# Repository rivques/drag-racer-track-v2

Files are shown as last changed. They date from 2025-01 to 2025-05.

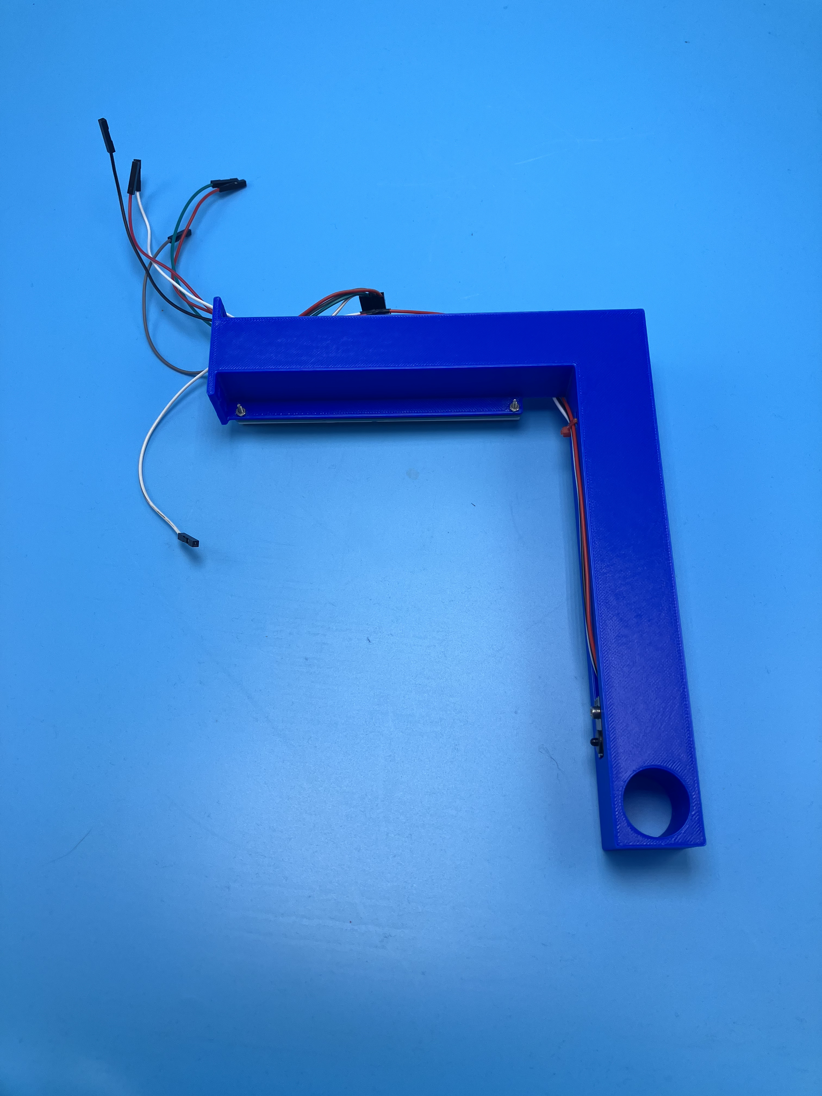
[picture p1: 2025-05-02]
doc-pics/end_cap_left_assembled_back.jpg

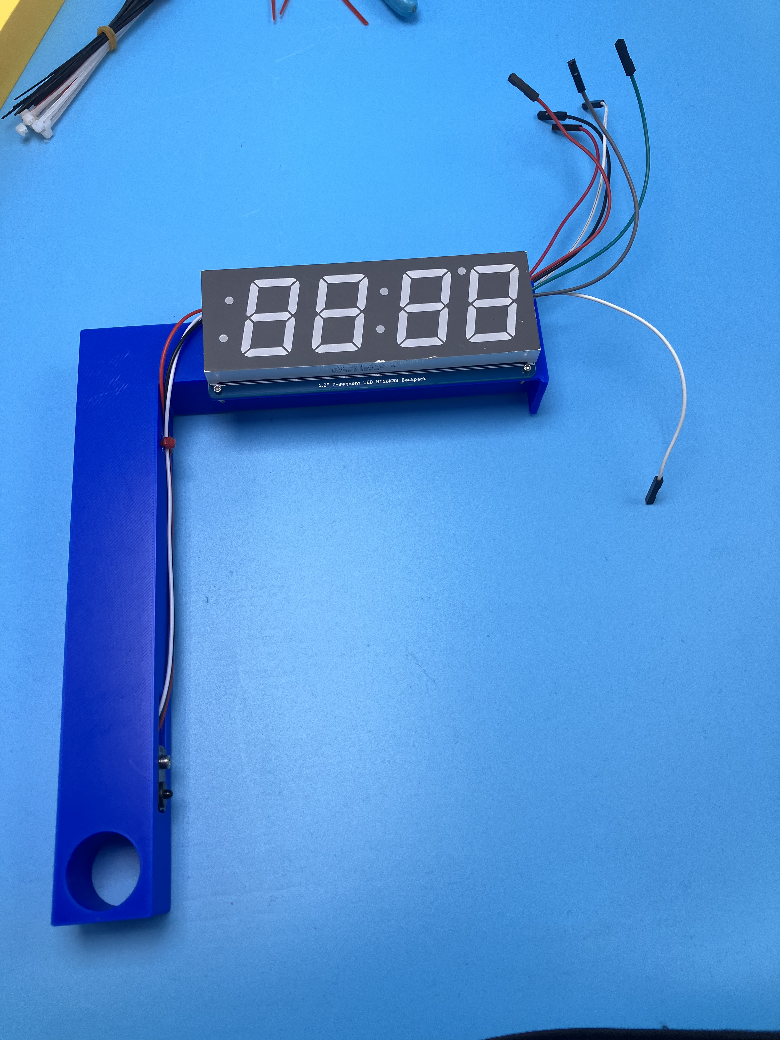
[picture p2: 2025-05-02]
doc-pics/end_cap_left_assembled_front.jpg

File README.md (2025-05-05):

# drag-racer-track-v2
A new and improved version of [mini-drag-racetrack](https://github.com/rivques/mini-drag-racetrack).
A photo of the complete assembly

## Contact Me
While this racetrack was designed to be maintainable by people other than me, please don't hesitate to contact me if you run into an issue that these docs don't cover.
You can open an issue on this repository, email me at `web (at) rivques (dot) dev`, or check [my website](https://rivques.dev) for my latest contact information.

## Troubleshooting
See [troubleshooting.md](docs/troubleshooting.md)

## How to Use
See [how_to_use.md](docs/how_to_use.md)

## Bill Of Materials
See [bill_of_materials.md](docs/bill_of_materials.md)

## Assembly From Storage
See [assembly_from_storage.md](docs/assembly_from_storage.md)

## Assembly From Scratch
See [assembly_from_scratch.md](docs/assembly_from_scratch.md)

## CAD
See [the CAD folder](https://github.com/rivques/drag-racer-track-v2/tree/main/cad) or [this Onshape document](https://cvilleschools.onshape.com/documents/214ca204c2fbd1332e8a9828/w/7c57c6410ddb9c7d8c5eff08/e/c34b4d3245393d7aa3c3b2bb).

## Project Proposal
Available at [this Google doc](https://docs.google.com/document/d/1fPM3jAb2btpLcQTNEUYPZXAGJ7guPSih1aArkj4l1_s/edit?usp=sharing), viewable from a CCS account.

## Photos
Various photos of the assembly are available in the [doc-pics](https://github.com/rivques/drag-racer-track-v2/tree/main/doc-pics) directory.

## Circuit Diagrams
Schematics and board layouts are available in the [circuit/outputs](https://github.com/rivques/drag-racer-track-v2/tree/main/circuit/outputs) directory.

### Commmunication
The three modules communicate over straight-through CAT-5 (aka Ethernet) cable. This pinout is constructed to allow near-unambiguous determination by the main processor of 1. if a cable is connected and 2. if the cable is connected to the motors or the screen.

The pinout is as follows (assuming T568A terminations):

#### Main-Motor (purpose and direction from Main's perspective):

RJ-45 Pin # | T568A color | Pico pin | Purpose | Direction | Notes
---|---|---|---|---|---
1|Wh/Gr|GND|GND|Bidirectional|Shared ground reference
2|Gr|GP0|TX|OUTPUT|UART 8N1@9600 baud
3|Wh/Or|GP2|Discrim|INPUT|Tied to GND at Motor
4|Bl|NC|NC||
5|Wh/Bl|3V3OUT|3V3|OUTPUT|
6|Or|GP1|RX|INPUT|UART 8N1@9600 baud
7|Wh/Br|GP3|Presence|INPUT|Tied to GND at Motor
8|Br|NC|NC||

#### Main-Button Controller (purpose and direction from Main's perspective):

RJ-45 Pin # | T568A color | Pico pin | Purpose | Direction | Notes
---|---|---|---|---|---
1|Wh/Gr|GND|GND|OUTPUT|
2|Gr|GP17|LED_RACE|OUTPUT|
3|Wh/Or|GP8|Discrim|INPUT|Tied to RESET at Controller
4|Bl|GP4|RESET|INPUT|
5|Wh/Bl|GP16|LED_ARM|OUTPUT|
6|Or|GP5|ARM|INPUT|
7|Wh/Br|GP7|Presence|INPUT|Tied to GND at Controller
8|Br|GP6|RACE|INPUT|

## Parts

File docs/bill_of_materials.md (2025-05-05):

# Bill of Materials

## Electronics

* 1x Mainboard PCB. For KiCad files, see the circuit directory of this repo.
* 2x [Adafruit beam-break 3mm sensors](https://www.adafruit.com/product/2167)
* 4x [SparkFun RJ45 breakouts](https://www.sparkfun.com/sparkfun-rj45-breakout.html) with [SparkFun RJ45 conectors](https://www.sparkfun.com/rj45-8-pin-connector.html)
* 2x [Adafruit 1.2" 4x7 segment LED displays w/ I2C backpack](https://www.adafruit.com/product/1269)
* 1x [Adafruit 1.3" OLED display](https://www.adafruit.com/product/938)
* 2x [SPDT breadboard switch](https://www.adafruit.com/product/805)
* 2x [Raspberry Pi Pico](https://www.adafruit.com/product/5525)
* 2x [1N4001 diodes](https://www.adafruit.com/product/755)
* 1x [7805 voltage regulator](https://www.adafruit.com/product/2164)
* 1x 0.22-0.33µF capacitor
* 1x 0.1µF capacitor
* 11x 220Ω resistors
* 5x single-color LEDs
* 3x [COMMON ANODE RGB LEDs](https://www.adafruit.com/product/302)
* 1x [2cm x 8cm perfboard](https://www.adafruit.com/product/4783)
* 1x [3cm x 7cm perfboard](https://www.adafruit.com/product/4784)
* 3x [12mm breadboard pushbuttons](https://www.adafruit.com/product/1119), with the bottom nubs snipped off so they lay flat
* 1x [Adafruit Perma-Proto Bonnet Mini](https://www.adafruit.com/product/3203)
* 2x [micro servos](https://www.adafruit.com/product/169)
* 1x [piezo buzzer](https://www.adafruit.com/product/160)
* 1x [4xAA battery holder](https://www.adafruit.com/product/3859)
* 1x 9V battery clip
* 2x Ethernet cables, one at least 13 feet long
* Assorted DuPont headers

## 3D-printed parts

From [the CAD folder](https://github.com/rivques/drag-racer-track-v2/tree/main/cad) or [this Onshape document](https://cvilleschools.onshape.com/documents/214ca204c2fbd1332e8a9828/w/7c57c6410ddb9c7d8c5eff08/e/c34b4d3245393d7aa3c3b2bb):

* end_cap_left
* end_cap_center
* end_cap_right
* start_cap_left
* start_cap_center
* start_cap_right

All of these should fit on a Prusa MK4S and can be printed out of PLA. Each should have a fairly obviously correct orientation. They shouldn't need supports.

## Other parts

* 12x #4-40 McMaster heat-set inserts
* Assorted 1/2in #4-40 standoffs
* Assorted #4-40 bolts (including button caps for the battery pack)

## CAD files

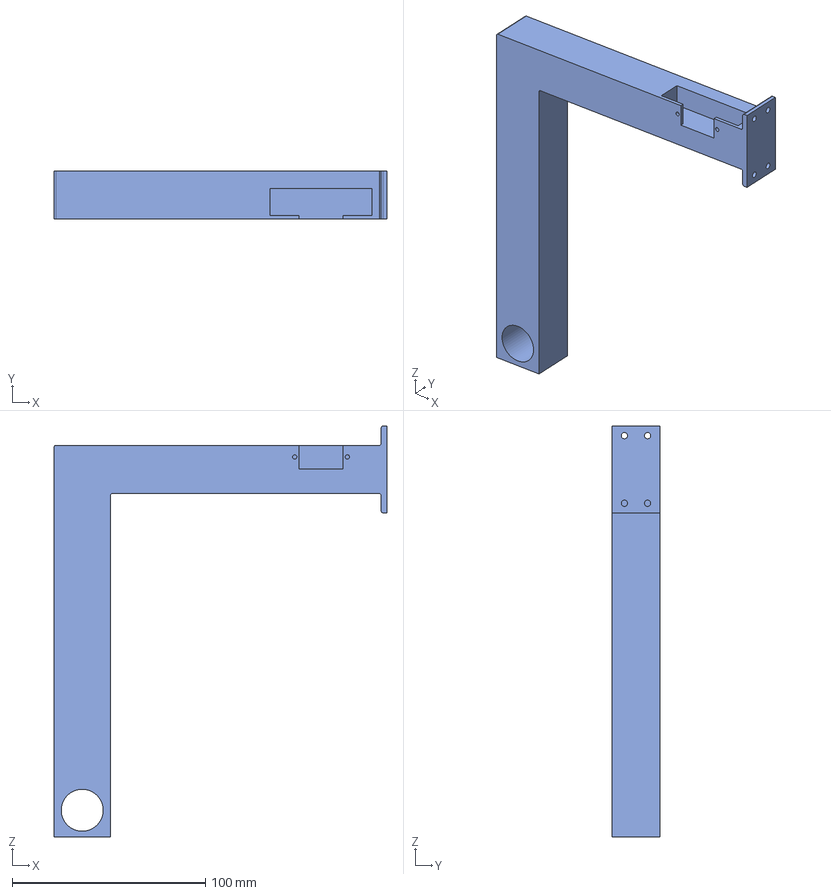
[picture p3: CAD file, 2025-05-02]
cad/start_cap_left.step
172.4 x 25.0 x 212.8 mm

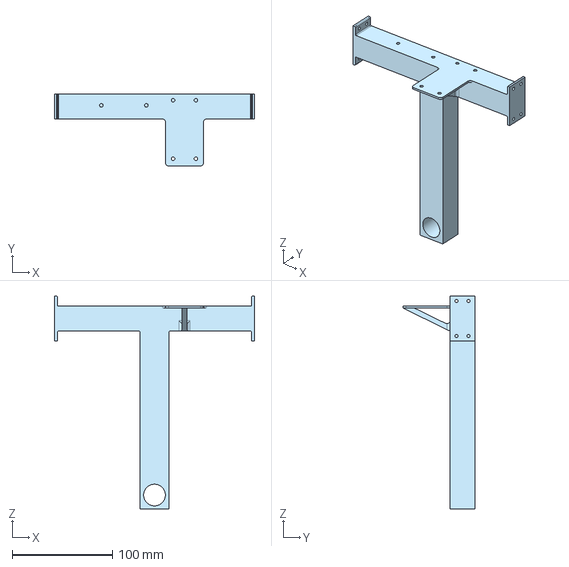
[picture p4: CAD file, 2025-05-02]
cad/start_cap_center.step
200.0 x 71.9 x 212.8 mm

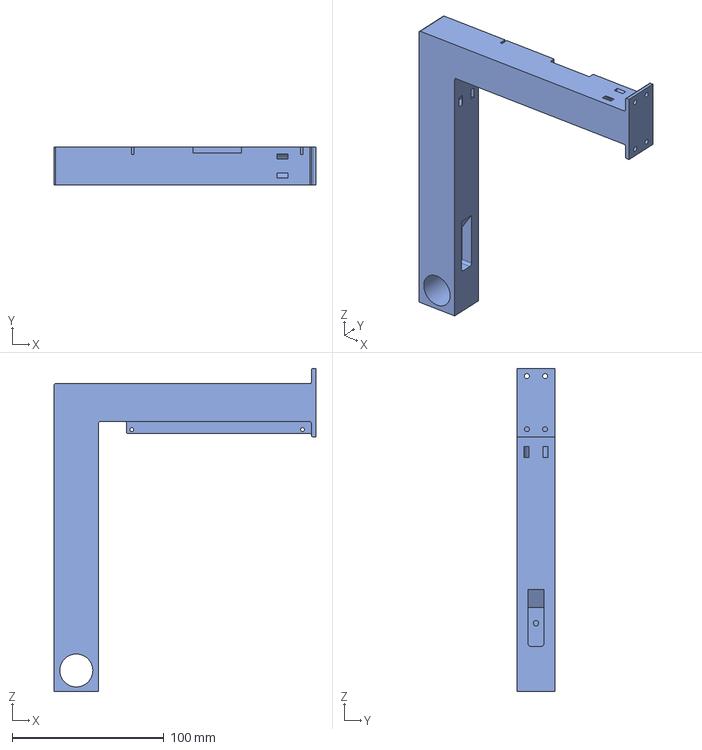
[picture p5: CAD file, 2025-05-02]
cad/end_cap_left.step
172.4 x 25.0 x 212.8 mm

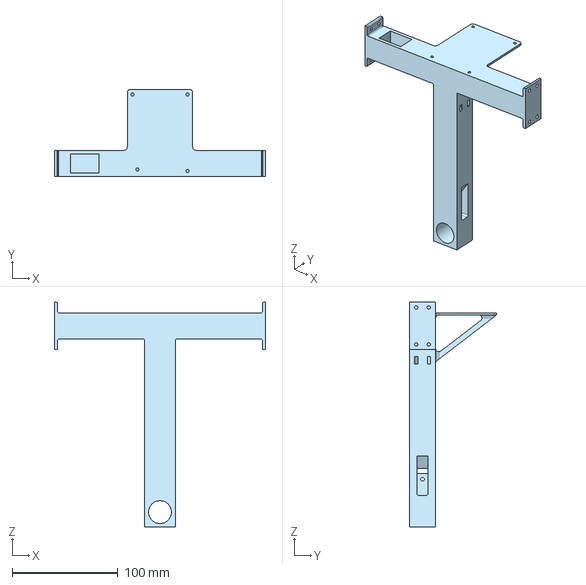
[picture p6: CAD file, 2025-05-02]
cad/end_cap_center.step
200.0 x 82.8 x 212.8 mm

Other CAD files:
cad/start_cap_right.step
cad/end_cap_right.step

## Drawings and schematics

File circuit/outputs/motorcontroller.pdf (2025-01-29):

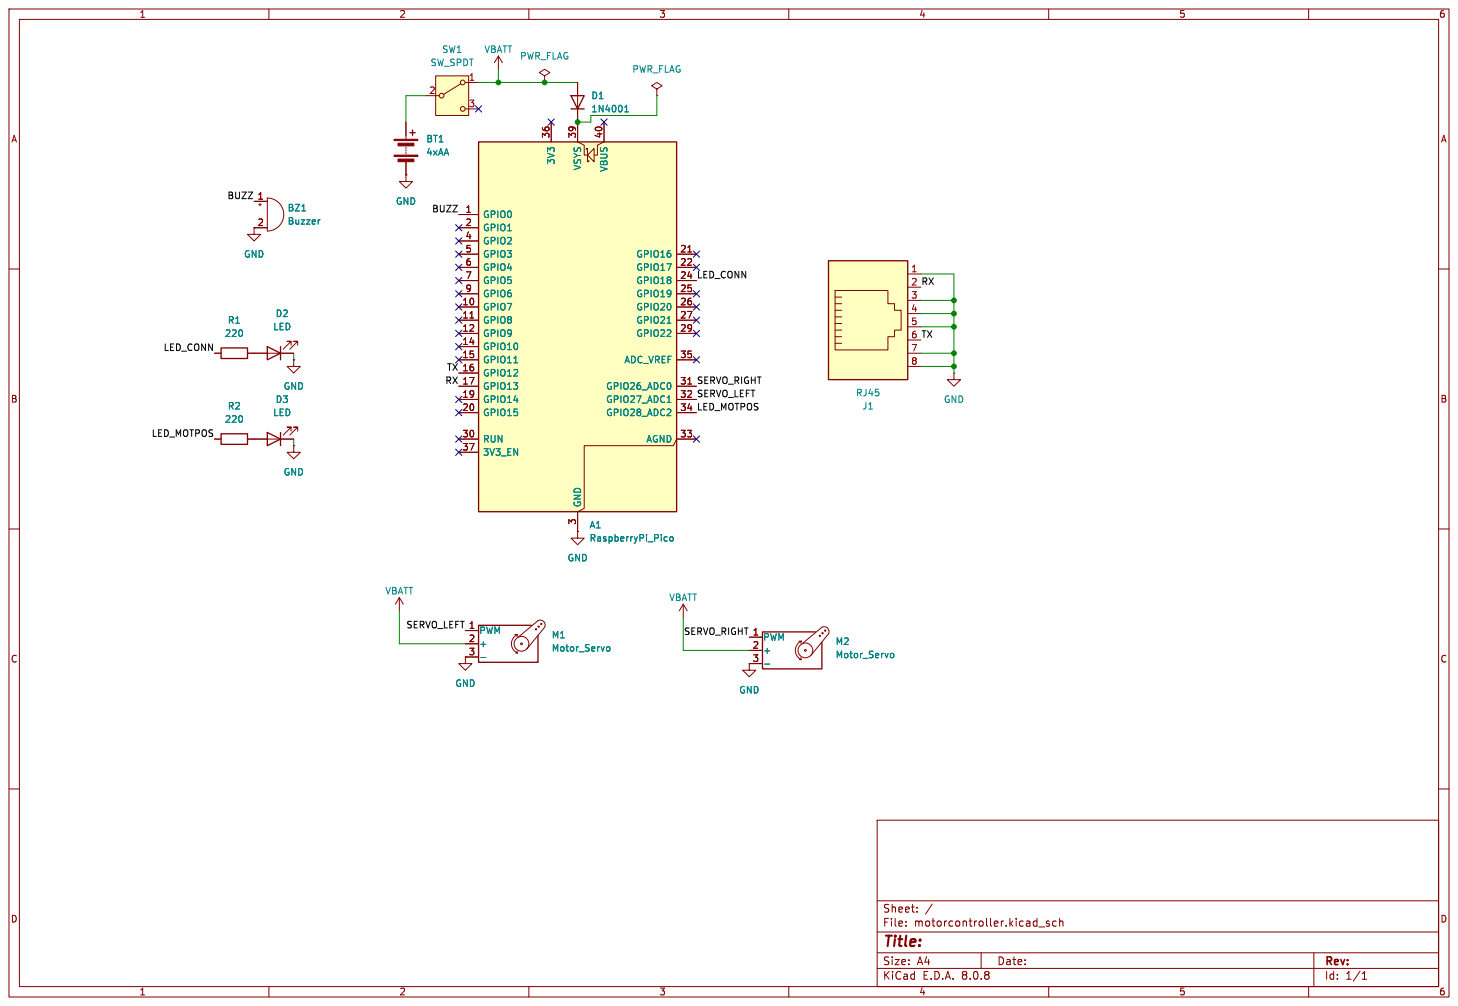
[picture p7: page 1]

Id: 1/1 Title: File: motorcontroller.kicad_sch Sheet: /

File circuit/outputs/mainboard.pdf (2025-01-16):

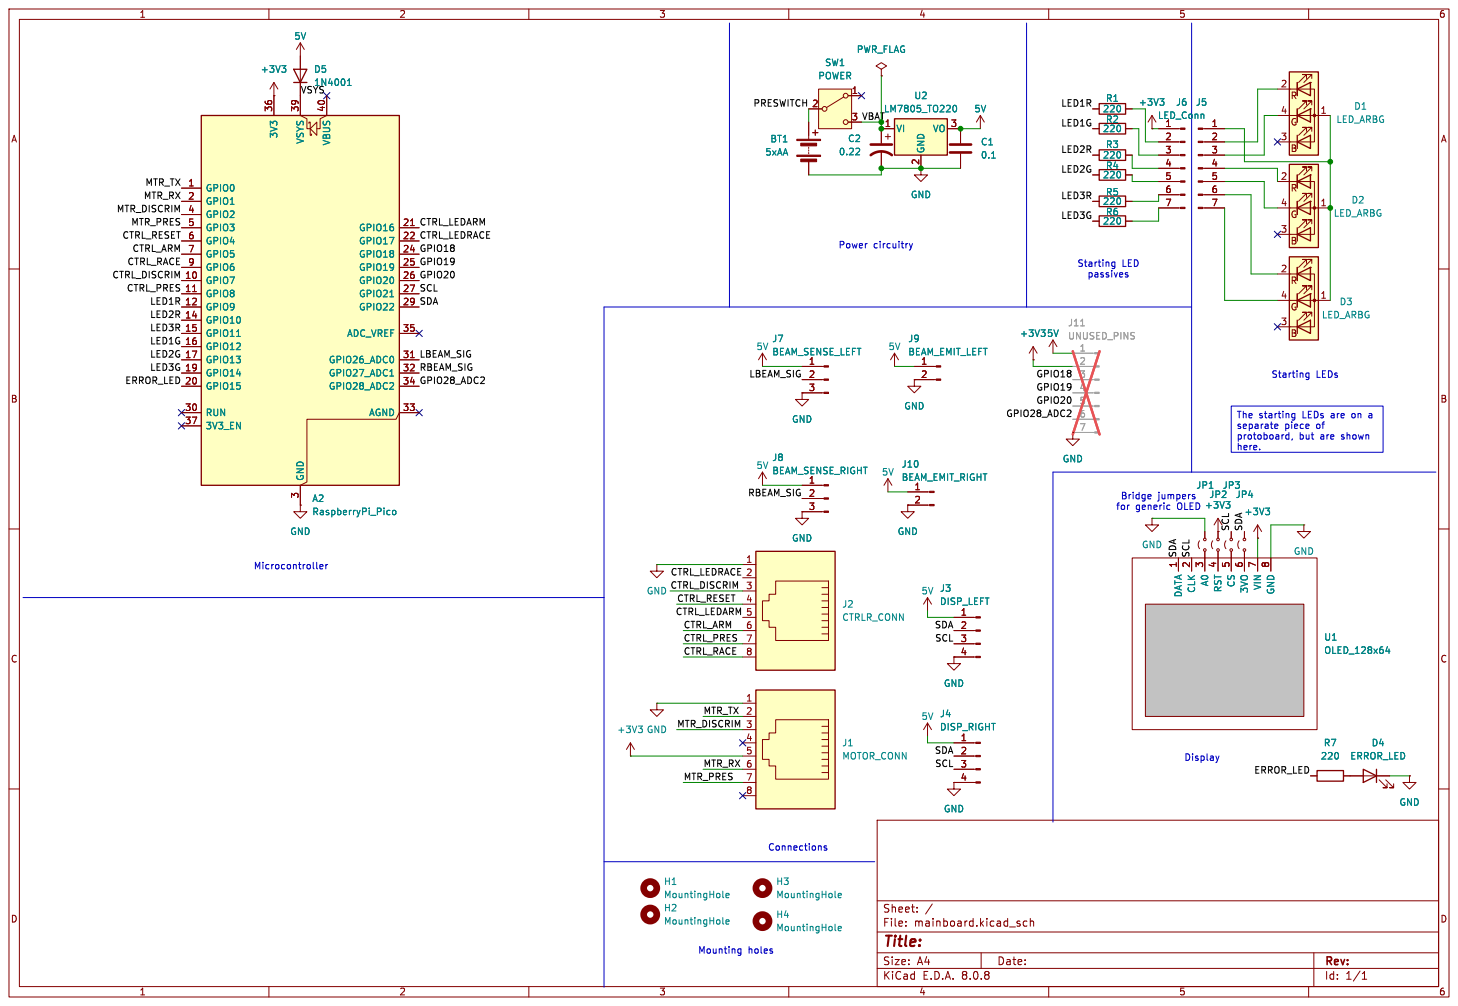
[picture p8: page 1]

+3V3 H3 MountingHole H4 MountingHole H1 MountingHole GND

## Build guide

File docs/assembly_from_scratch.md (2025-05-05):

# Assembly From Scratch

This document describes how to assemble the racetrack from scratch. If you're just assembling from storage, see [assembly_from_storage.md](../docs/assembly_from_storage.md).

## Parts

See [the bill of materials](../docs/bill_of_materials.md) for a list of parts.

## Electronics

### Motor controller

1. Solder an Adafruit Perma-Proto Bonnet Mini according to the [wiring diagram](../circuit/outputs/motorcontrollerwiring.png). [Here](../doc-pics/motorcontroller-bottom.jpg) are [some](../doc-pics/motorcontroller-top-withoutpico.jpg) [pictures](../doc-pics/motorcontroller-top-withpico.jpg) of what it should look like (albeit without the battery and switch).

### Mainboard

1. If you're using a generic OLED instead of an Adafruit OLED, bridge the jumpers on the mainboard PCB accordingly.
2. Solder headers and breakout boards to the mainboard PCB according to the [schematic](../circuit/outputs/mainboard.pdf). I reccommend soldering female headers to the board for the Pico, RJ45 breakout and OLED but you can choose to solder them directly to the board if you wish.
3. Run a bodge wire from GP20 on the unused pins header to an SDA pin. This corrects for the board incorrectly wiring GP22 to SDA.

### LED board

1. Solder 3 common-anode RGB LEDs to a strip of protoboard. Break out their anodes, red, and green pins to a header according to the silkscreened label on the mainboard PCB.

### Race controller

1. Solder a piece of protoboard according to the [wiring diagram](../circuit/outputs/racecontroller.excalidraw.png).
2. Label the buttons with a labelmaker.

## Structure

1. Print out the 3D-printed parts.
2. Using a soldering iron, insert the heat-set inserts. It may help to slightly counterbore the holes with a 1/8in bit, to help the inserts seat. It's important that the inserts go in as straight as possible.
3. Modify the beam-break sensors by carefully drilling out their bolt holes to 1/8 in. Then, for the emitters, terminate their wires with a female DuPont connector. For the receivers, extend their wires to ~320mm and terminate with female DuPont.
4. Bolt the various electronics onto the 3D-printed frame. The mainboard, motor controller, and LED board are installed on standoffs. 
5. Neaten up the cables with zip ties.
6. Bolt the pieces together and connect the electronics to the mainboard according to the silkscreened pinouts.

See [the pictures](https://github.com/rivques/drag-racer-track-v2/tree/main/doc-pics) for several pictures of the final assembly.

By this point you have all the subassemblies needed to follow [the assembly from storage instructions](../docs/assembly_from_storage.md).

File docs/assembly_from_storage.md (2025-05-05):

# Assembly From Storage

This document describes how to assemble the racetrack from its storage configuration.

## Parts

You should have the following subassemblies:

* End cap with attached mainboard, screens, beam-break sensors, etc.
* Start cap with attached motor board, servos, etc.
* Race control board
* 6x 5ftx3/4in PVC pipe
* 3 PVC couplers
* 2x Ethernet cables, one at least 13 feet long
* Some scraps of paper
* a bit of tape

## Assembly

1. Put 3 PVC pipes into the holes in the start cap.
2. Add couplers to those pipes and extend each with another PVC pipe.
3. Put the end cap on the other end of the PVC pipes.
4. Attach the motor RJ-45 port of the mainboard to the motor control board. You can run it through the middle PVC pipe.
5. Attach the controller RJ-45 port of the mainboard to the race controller.
6. Tape the scraps of paper to the servo arms, to act as photointerruptor triggers.

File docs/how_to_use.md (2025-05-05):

# How to Use
If something goes wrong at any point, check [the troubleshooting guide](../docs/troubleshooting.md).

## Setup

1. Power on both the mainboard and the race controller.
2. Wait for the mainboard to show IDLE on its display.

## Run a Race

1. Press Arm on the race controller. The servo motors should lower.
2. Set up the drag racers under the servo motors.
3. Press Race. The countdown lights go off and the servos lift.
4. To end the race early (e.g. if a racer breaks down), press Reset.

## Power Off

1. Turn off BOTH the mainboard and the motor controller.

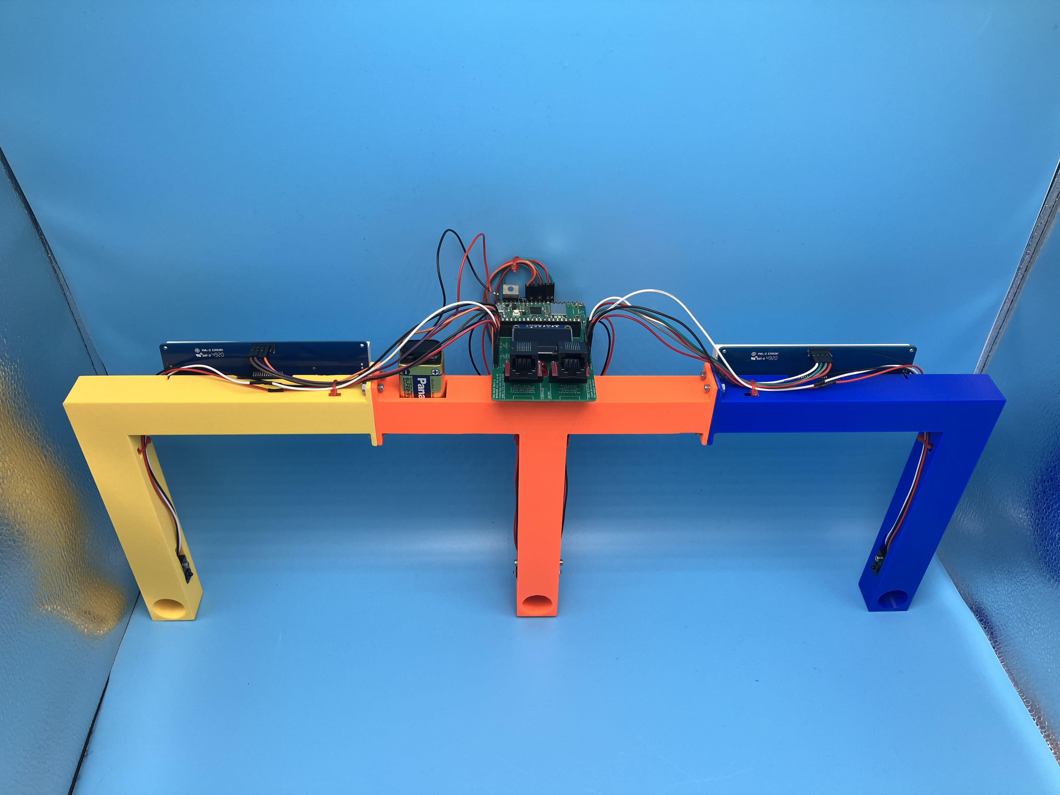
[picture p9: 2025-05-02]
doc-pics/end_cap_assembled_topback.jpg

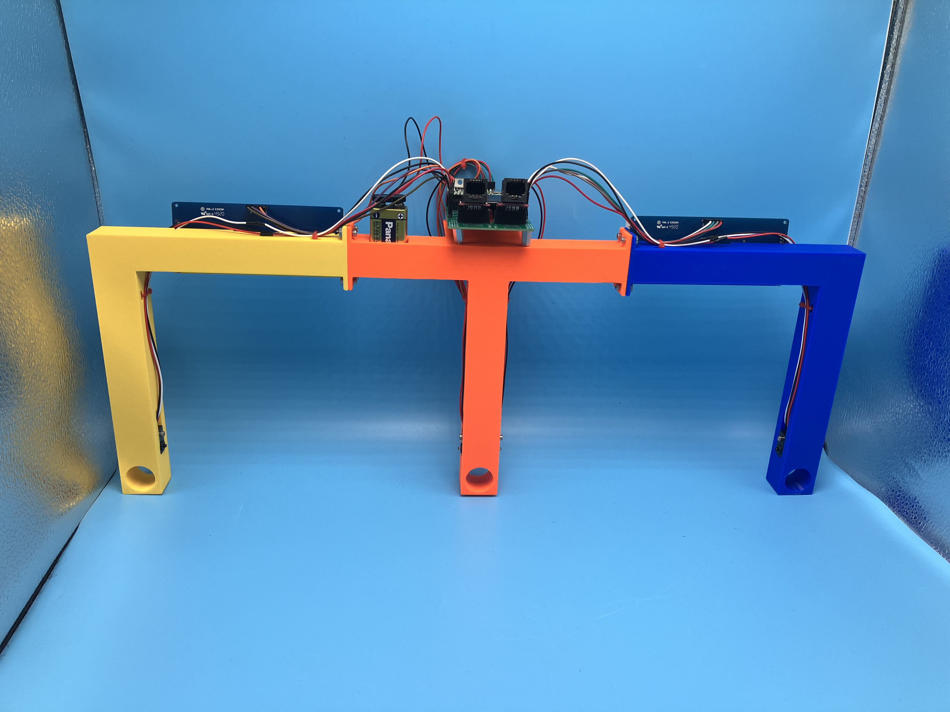
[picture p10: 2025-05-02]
doc-pics/end_cap_assembled_back.jpg

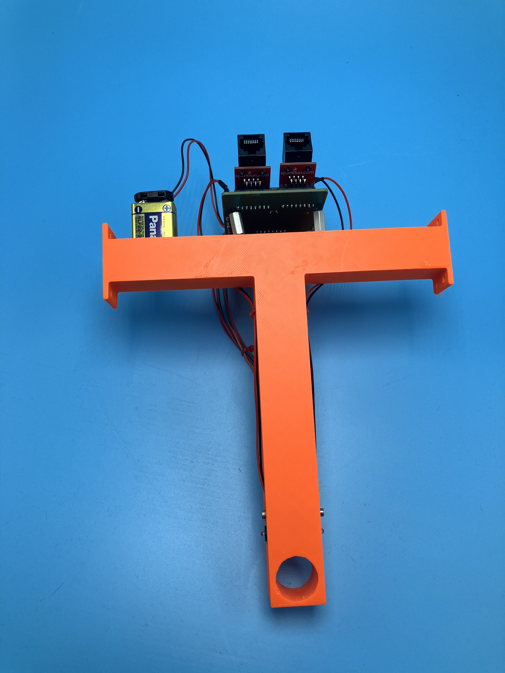
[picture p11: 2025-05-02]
doc-pics/end_cap_center_assembled_back.jpg

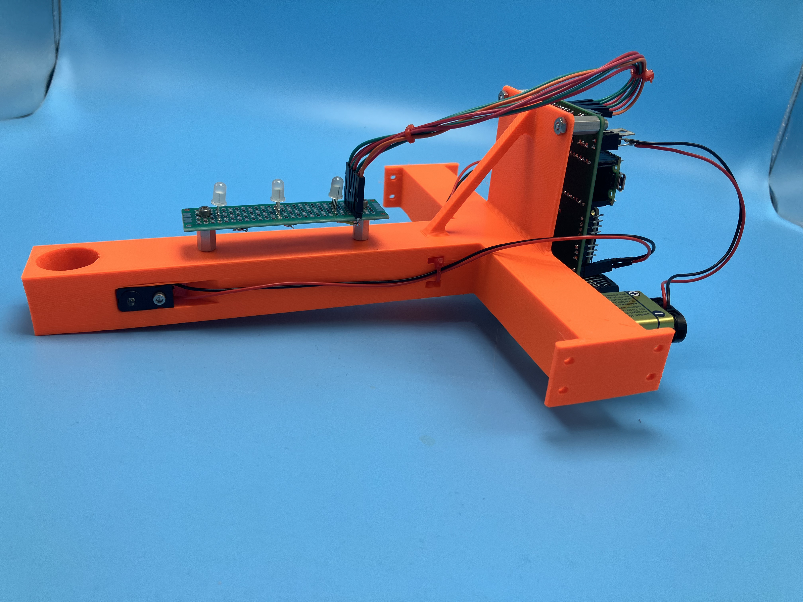
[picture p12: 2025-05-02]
doc-pics/end_cap_center_assembled_side.jpg

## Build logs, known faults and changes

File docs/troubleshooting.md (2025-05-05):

# Troubleshooting

## I'm getting an error code!

error code|problem|resolution
---|---|---
100|The left time display is not found.|Check that the wiring to the left display is accurate. Failing that, check that the battery is full.
101|The right time display is not found.|Check that the wiring to the right display is accurate. Failing that, check that the battery is full.
200|The race controller is unplugged.|Plug in the race controller. Failing that, check the ethernet cable. Failing that, check that the race controller's circuitry is accurate and not shorted.
201|The motor controller is plugged into the race controller port.|Plug the motor controller into the correct port. Failing that, check the ethernet cable.
300|The motor controller is unplugged.|Plug in the motor controller. Failing that, check the ethernet cable. Failing that, check that the motor controller's circuitry is accurate and not shorted.
301|The race controller is plugged into the motor controller port.|Plug the race controller into the correct port. Failing that, check the ethernet cable.
302|The motor controller is plugged in, but the race controller can't communicate with it.|Check that the motor controller is turned on. Failing that, check the ethernet cable.

## The mainboard is not powering on!

* Check that the battery is full. 
* Check that there is no short-circuit at the battery input.

## The motor controller is beeping!

* This means that it cannot communicate with the mainboard.
* Check that the mainboard is powered on.
* If the mainboard is showing an error code, resolve the error code.

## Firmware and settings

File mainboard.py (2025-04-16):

import board
import digitalio
import asyncio
import displayio
import terminalio
import adafruit_displayio_ssd1306
import busio
from adafruit_ht16k33 import segments
from lib.errors import ErrorType, Error
import time
from adafruit_display_text import text_box

class Mainboard:
    def __init__(self):
        # state
        self.state = "IDLE" # IDLE, ARMED, COUNTDOWN, RACING

        self.error_type = ErrorType.NONE
        self.error = None

        self.race_start_time = 0
        self.left_finish_time = 0
        self.right_finish_time = 0

        self.controller_state = "UNPLUGGED"
        self.motor_state = "UNPLUGGED"
        self.last_motor_packet_time = 0

        # set up buses
        displayio.release_displays()
        i2c = busio.I2C(board.GP21, board.GP20)
        self.uart = busio.UART(board.GP0, board.GP1, baudrate=9600)
    
        # error hardware
        self.error_led = digitalio.DigitalInOut(board.GP15)
        self.error_led.direction = digitalio.Direction.OUTPUT
        self.error_led.value = False
        error_display_bus = displayio.I2CDisplay(i2c, device_address=0x3D)
        self.error_display = adafruit_displayio_ssd1306.SSD1306(error_display_bus, width=128, height=64)
        self.error_display_text = text_box.TextBox(terminalio.FONT, width=128, height=64, align=text_box.TextBox.ALIGN_CENTER, text="Starting up...", y=12)
        self.error_display.root_group = self.error_display_text
        
        # time display hardware
        try:
            self.left_time_display = segments.BigSeg7x4(i2c, address=0x70)
        except ValueError:
            self.error_type = ErrorType.FATAL
            self.error = Error(100, "Left time display is not found")
        try:
            self.right_time_display = segments.BigSeg7x4(i2c, address=0x71)
        except ValueError:
            self.error_type = ErrorType.FATAL
            self.error = Error(101, "Right time display is not found")
        self.starting_leds = []
        for red_pin, green_pin in [(board.GP9, board.GP12), (board.GP10, board.GP13), (board.GP11, board.GP14)]:
            red_led = digitalio.DigitalInOut(red_pin)
            red_led.direction = digitalio.Direction.OUTPUT
            red_led.value = False
            green_led = digitalio.DigitalInOut(green_pin)
            green_led.direction = digitalio.Direction.OUTPUT
            green_led.value = False
            self.starting_leds.append((red_led, green_led))
        
        # beam watch hardware
        self.left_beam = digitalio.DigitalInOut(board.GP26)
        self.left_beam.direction = digitalio.Direction.INPUT
        self.left_beam.pull = digitalio.Pull.UP
        self.right_beam = digitalio.DigitalInOut(board.GP27)
        self.right_beam.direction = digitalio.Direction.INPUT
        self.right_beam.pull = digitalio.Pull.UP

        # controller hardware
        self.reset_button = digitalio.DigitalInOut(board.GP4)
        self.reset_button.direction = digitalio.Direction.INPUT
        self.reset_button.pull = digitalio.Pull.UP
        self.race_button = digitalio.DigitalInOut(board.GP6)
        self.race_button.direction = digitalio.Direction.INPUT
        self.race_button.pull = digitalio.Pull.UP
        self.arm_button = digitalio.DigitalInOut(board.GP5)
        self.arm_button.direction = digitalio.Direction.INPUT
        self.arm_button.pull = digitalio.Pull.UP
        self.controller_presence = digitalio.DigitalInOut(board.GP8)
        self.controller_presence.direction = digitalio.Direction.INPUT
        self.controller_presence.pull = digitalio.Pull.UP
        self.controller_discrim = digitalio.DigitalInOut(board.GP7)
        self.controller_discrim.direction = digitalio.Direction.INPUT
        # no pull for controller discrim
        self.arm_led = digitalio.DigitalInOut(board.GP16)
        self.arm_led.direction = digitalio.Direction.OUTPUT
        self.arm_led.value = True
        self.race_led = digitalio.DigitalInOut(board.GP17)
        self.race_led.direction = digitalio.Direction.OUTPUT
        self.race_led.value = False

        # motor hardware
        self.motor_presence = digitalio.DigitalInOut(board.GP3)
        self.motor_presence.direction = digitalio.Direction.INPUT
        self.motor_presence.pull = digitalio.Pull.UP
        self.motor_discrim = digitalio.DigitalInOut(board.GP2)
        self.motor_discrim.direction = digitalio.Direction.INPUT
        # no pull for motor discrim
    
    # state for error display
    last_error_code = 0
    last_state = "NONE"
    async def run_error_display(self):
        while True:
            if self.error_type == ErrorType.NONE and (self.last_error_code != 0 or self.last_state != self.state):
                self.error_led.value = False
                self.error_display_text.text = "Drag Racer Track V2\n"+ self.state
                self.last_error_code = 0
                self.last_state = self.state
            elif self.error_type != ErrorType.NONE:
                self.error_led.value = True
                if self.error.error_code != self.last_error_code:
                    self.last_error_code = self.error.error_code
                    print("new error")
                    self.error_display_text.text = f"{'RECOVERABLE' if self.error_type == ErrorType.RECOVERABLE else "FATAL"} Error: Code {self.error.error_code}\n{self.error.short_msg}\nSEE DOCS FOR MORE"
                if self.error_type == ErrorType.RECOVERABLE:
                    await self.blink_error_led()
            await asyncio.sleep(0)
    
    async def blink_error_led(self):
        while self.error_type == ErrorType.RECOVERABLE:
            self.error_led.value = True
            await asyncio.sleep(0.5)
            self.error_led.value = False
            await asyncio.sleep(0.5)
    
    async def manage_input(self):
        while True:
            await asyncio.sleep(0)
            old_state = self.controller_state
            if self.controller_presence.value == True:
                self.controller_state = "UNPLUGGED"
                if not self.error:
                    self.error_type = ErrorType.RECOVERABLE
                    self.error = Error(200, "Controller unplugged")
            else:
                self.controller_state = "PLUGGED"
                # we're plugged in
                if old_state == "UNPLUGGED":
                    # clear the error if it was set
                    if self.error and self.error.error_code == 200:
                        self.error_type = ErrorType.NONE
                        self.error = None
                    # check if discrim is correct
                    if self.controller_discrim.value == False:
                        if not self.error:
                            self.error_type = ErrorType.RECOVERABLE
                            self.error = Error(201, "Motor port wrong")
                            continue
                    else:
                        if self.error and self.error.error_code == 201:
                            self.error_type = ErrorType.NONE
                            self.error = None
                # by this point we've confirmed we have the correct cable in the correct port
                # don't do anything if there's an error
                if self.error_type != ErrorType.NONE:
                    continue
                # ok, _now_ we're free to respond to button presses
                if self.state == "IDLE":
                    if self.arm_button.value == False:
                        self.state = "ARMED"
                        # clear times
                        self.left_finish_time = 0
                        self.right_finish_time = 0
                    # we can't do anything else in IDLE
                elif self.state == "ARMED":
                    if self.race_button.value == False:
                        self.state = "COUNTDOWN"
                    if self.reset_button.value == False:
                        self.state = "IDLE"
                elif self.state == "COUNTDOWN":
                    if self.reset_button.value == False:
                        # when resetting out of countdown, go back to armed (b/c going to idle would release racers which is prob not user intent)
                        self.state = "ARMED"
                        # turn off the LEDs
                        for red_led, green_led in self.starting_leds:
                            red_led.value = True
                            green_led.value = True
                elif self.state == "RACING":
                    if self.reset_button.value == False:
                        self.state = "IDLE"
    
    async def blink_controller_leds(self):
        last_blink = time.monotonic()
        while True:
            await asyncio.sleep(0)
            if self.controller_state == "UNPLUGGED":
                self.arm_led.value = True
            else:
                if self.error_type != ErrorType.NONE:
                    # alternating fast blinks
                    if last_blink + 0.1 < time.monotonic():
                        self.race_led.value = self.arm_led.value
                        self.arm_led.value = not self.arm_led.value
                        last_blink = time.monotonic()
                elif self.state == "IDLE":
                    # arm blinking
                    self.race_led.value = False
                    if last_blink + 0.5 < time.monotonic():
                        self.arm_led.value = not self.arm_led.value
                        last_blink = time.monotonic()
                elif self.state == "ARMED":
                    # arm solid, race blinking
                    self.arm_led.value = True
                    if last_blink + 0.5 < time.monotonic():
                        self.race_led.value = not self.race_led.value
                        last_blink = time.monotonic()
                elif self.state == "COUNTDOWN":
                    # synced fast blinking
                    if last_blink + 0.25 < time.monotonic():
                        self.arm_led.value = not self.race_led.value
                        self.race_led.value = not self.race_led.value
                        last_blink = time.monotonic()
                elif self.state == "RACING":
                    # arm off, race blinking
                    self.arm_led.value = False
                    if last_blink + 0.5 < time.monotonic():
                        self.race_led.value = not self.race_led.value
                        last_blink = time.monotonic()        
    
    async def watch_beams(self):
        while True:
            await asyncio.sleep(0)
            if self.state == "RACING":
                if self.left_beam.value == False and self.left_finish_time == 0:
                    self.left_finish_time = time.monotonic()
                if self.right_beam.value == False and self.right_finish_time == 0:
                    self.right_finish_time = time.monotonic()
                if self.left_finish_time > 0 and self.right_finish_time > 0:
                    self.state = "IDLE"

    async def run_time_display(self):
        def format_time(seconds):
            return f"{int(seconds):02}:{int(seconds*100%100):02}"
        while True:
            await asyncio.sleep(0)
            if self.state == "IDLE":
                for red_led, green_led in self.starting_leds:
                    red_led.value = True
                    green_led.value = True
                if not self.left_finish_time:
                    self.left_time_display.print(" DnF")
                if not self.right_finish_time:
                    self.right_time_display.print(" DnF")
            elif self.state == "ARMED":
                self.left_time_display.print("00:00")
                self.right_time_display.print("00:00")
                for red_led, green_led in self.starting_leds:
                    red_led.value = True
                    green_led.value = True
            elif self.state == "COUNTDOWN":
                # here the standard flow of this loop is broken, this is the entire countdown sequence
                # also these LEDs are common anode so False is on and True is off
                self.starting_leds[0][0].value = False
                await asyncio.sleep(0.5)
                if self.state != "COUNTDOWN":
                    # check if we reset mid-countdown
                    continue
                self.starting_leds[1][0].value = False
                await asyncio.sleep(0.5)
                if self.state != "COUNTDOWN":
                    continue
                self.starting_leds[2][0].value = False
                await asyncio.sleep(0.5)
                if self.state != "COUNTDOWN":
                    continue
                # RACE STARTS HERE
                self.state = "RACING"
                for red_led, green_led in self.starting_leds:
                    red_led.value = True
                    green_led.value = False
                self.race_start_time = time.monotonic()
                self.left_finish_time = 0
                self.right_finish_time = 0
            elif self.state == "RACING":
                elapsed = time.monotonic() - self.race_start_time
                if self.left_finish_time:
                    self.left_time_display.print(format_time(self.left_finish_time - self.race_start_time))
                else:
                    self.left_time_display.print(format_time(elapsed))
                if self.right_finish_time:
                    self.right_time_display.print(format_time(self.right_finish_time - self.race_start_time))
                else:
                    self.right_time_display.print(format_time(elapsed))
   
    async def manage_motors(self):
        while True:
            await asyncio.sleep(0.1)
            old_state = self.motor_state
            if self.motor_presence.value == True:
                self.motor_state = "UNPLUGGED"
                if not self.error:
                    self.error_type = ErrorType.RECOVERABLE
                    self.error = Error(300, "Motor unplugged")
            else:
                self.motor_state = "PLUGGED"
                # we're plugged in
                if old_state == "UNPLUGGED":
                    # clear the error if it was set
                    if self.error and self.error.error_code == 300:
                        self.error_type = ErrorType.NONE
                        self.error = None
                    # check if discrim is correct
                    if self.motor_discrim.value == True:
                        if not self.error:
                            self.error_type = ErrorType.RECOVERABLE
                            self.error = Error(301, "Motor port wrong")
                            continue
                    else:
                        if self.error and self.error.error_code == 301:
                            self.error_type = ErrorType.NONE
                            self.error = None
                # by this point we've confirmed we have the correct cable in the correct port
                packet = ""
                while self.uart.in_waiting:
                    self.last_motor_packet_time = time.monotonic()
                    packet += self.uart.read(1).decode()
                # we don't actually care about the packet, only that it exists
                if self.last_motor_packet_time + 1 < time.monotonic():
                    if not self.error:
                        self.error_type = ErrorType.RECOVERABLE
                        self.error = Error(302, "Motor not responding")
                else:
                    if self.error and self.error.error_code == 302:
                        self.error_type = ErrorType.NONE
                        self.error = None
                # tell the motor what to do
                if self.state == "IDLE":
                    self.uart.write(b"U")
                elif self.state == "ARMED":
                    self.uart.write(b"D")
                elif self.state == "COUNTDOWN":
                    self.uart.write(b"D")
                elif self.state == "RACING":
                    self.uart.write(b"U")

    
    async def run(self):
        if self.error_type != ErrorType.NONE:
            print("Error during init")
            await self.run_error_display() # display an error thatoccurred during init
        error_display_task = asyncio.create_task(self.run_error_display())
        input_task = asyncio.create_task(self.manage_input())
        controller_led_task = asyncio.create_task(self.blink_controller_leds())
        time_display_task = asyncio.create_task(self.run_time_display())
        motor_management_task = asyncio.create_task(self.manage_motors())
        beam_watch_task = asyncio.create_task(self.watch_beams())

        await asyncio.gather(error_display_task, input_task, controller_led_task, time_display_task, motor_management_task, beam_watch_task)

mainboard = Mainboard()
asyncio.run(mainboard.run())

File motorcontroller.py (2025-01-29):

# the software for the motor controllerboard. Listens to the mainboard over UART and controls the motors accordingly.

import board
import digitalio
import busio
import time
import asyncio
import pwmio

from adafruit_motor import servo

class MotorController():
    def __init__(self):
        self.conn_led = digitalio.DigitalInOut(board.GP18)
        self.conn_led.direction = digitalio.Direction.OUTPUT
        self.conn_led.value = False

        self.motor_led = digitalio.DigitalInOut(board.GP28)
        self.motor_led.direction = digitalio.Direction.OUTPUT
        self.motor_led.value = False

        self.buzzer = pwmio.PWMOut(board.GP0, frequency=440, duty_cycle=0)

        self.uart = busio.UART(board.GP12, board.GP13, baudrate=9600, receiver_buffer_size=1, timeout=0.05)
        self.connected = False
        self.last_packet_time = time.monotonic()

        servo_left_pwm = pwmio.PWMOut(board.GP27, frequency=50)
        self.servo_left = servo.Servo(servo_left_pwm)

        servo_right_pwm = pwmio.PWMOut(board.GP26, frequency=50)
        self.servo_right = servo.Servo(servo_right_pwm)

        self.motors_down = False
    
    async def manage_buzzer(self):
        # beep the buzzer if the connection is lost
        # this is intended as a battery-saving feature
        # to make sure the user doesn't turn off the mainboard
        # and forget about the motor controller
        while True:
            if not self.connected:
                self.buzzer.duty_cycle = 2**15
                await asyncio.sleep(0.5)
                self.buzzer.duty_cycle = 0
                await asyncio.sleep(0.5)
            else:
                self.buzzer.duty_cycle = 0

            await asyncio.sleep(0)

    async def manage_motors(self):
        # control the motors based on the state
        while True:
            if self.motors_down:
                self.servo_left.angle = 90
                self.servo_right.angle = 90
                self.motor_led.value = True
            else:
                self.servo_left.angle = 0
                self.servo_right.angle = 180
                self.motor_led.value = False

            await asyncio.sleep(0)
    
    async def comms_read(self):
        # watch the UART for incoming packets, and update the state accordingly
        while True:
            if self.uart.in_waiting:
                packet = self.uart.read(1)
                if packet == b'U':
                    self.motors_down = False
                elif packet == b'D':
                    self.motors_down = True
                else:
                    print("Invalid packet received")
                    continue
                self.last_packet_time = time.monotonic()
            
            # this logic looks a little weird because it has to interoperate with blink_conn_led
            # but it really just checks if the connection is alive and sets the led accordingly
            if self.last_packet_time + 1 < time.monotonic():
                if self.connected:
                    # connection was just lost
                    self.conn_led.value = False
                self.connected = False
            else:
                if not self.connected:
                    # connection was just established
                    self.conn_led.value = True
                self.connected = True
            await asyncio.sleep(0)

    async def blink_conn_led(self, time):
        # helper for comms_heartbeat
        # this logic looks a little weird because the led has to both communicate heartbeats and connection status
        print(f"blink_conn_led {time} (connected: {self.connected})")
        if self.connected:
            self.conn_led.value = False
        else:
            self.conn_led.value = True
        await asyncio.sleep(time)
        if self.connected: # re-check because it may have changed during the sleep
            self.conn_led.value = True
        else:
            self.conn_led.value = False

    async def comms_heartbeat(self):
        # send a heartbeat to the mainboard every 0.5sec
        # so that it knows this board is not only connected but alive
        while True:
            self.uart.write(b'HB')
            await self.blink_conn_led(0.1)
            await asyncio.sleep(0.4) # then wait for 0.4sec for a total of 2Hz heartbeat

    async def run(self):
        buzzer_task = asyncio.create_task(self.manage_buzzer())
        motor_task = asyncio.create_task(self.manage_motors())
        comms_read_task = asyncio.create_task(self.comms_read())
        comms_heartbeat_task = asyncio.create_task(self.comms_heartbeat())

        await asyncio.gather(buzzer_task, motor_task, comms_read_task, comms_heartbeat_task)


motor_controller = MotorController()
asyncio.run(motor_controller.run())

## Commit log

2025-01-14 test beam breaks and start planning wiring
2025-01-14 redo RJ45 wiring
2025-01-14 add pico pin columnn
2025-01-15 get started on schematic
    [mainboard.kicad_sch]
2025-01-15 schematic first pass
    [mainboard.kicad_sch]
2025-01-15 add LEDs to controller
    [mainboard.kicad_sch]
2025-01-15 kicad deleted some files ig lol
2025-01-15 add footprints and organize sheet
    [mainboard.kicad_sch]
2025-01-15 initial pcb layout
    [mainboard.kicad_pcb, mainboard.kicad_sch]
2025-01-15 route PCB
    [mainboard.kicad_pcb, mainboard.kicad_sch]
2025-01-15 refine PCB
    [mainboard-B_Cu.gbl, mainboard-B_Mask.gbs, mainboard-B_Paste.gbp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]
2025-01-16 This is the board that was produced as rev1
    [mainboard-B_Cu.gbl, mainboard-B_Mask.gbs, mainboard-B_Paste.gbp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]
2025-01-21 add circuit for motor controller
    [motorcontroller.kicad_pcb, motorcontroller.kicad_sch]
2025-01-22 add motor controller wiring diagram
    [motorcontroller.kicad_sch]
2025-01-23 adjust left servo wire
2025-01-24 move conn led and power connection
2025-01-24 update schematic to match wiring diagram
    [motorcontroller.kicad_sch]
2025-01-27 add some pics of the motor controller
2025-01-29 write motorcontroller firmware (half-tested)
2025-02-05 start making the physical board work
2025-02-06 fix short on motor controller board - oops
    [motorcontroller.kicad_sch]
2025-03-03 flip around motorcon rj45
2025-03-03 use a ground wire for that led
2025-03-14 add switch and power to motor controller
2025-03-19 add circuit for race controller
2025-04-16 small improvements + bugfixes to firmware
    [mainboard.py]
2025-04-17 reorganize docs and work on electronics BOM
2025-05-05 switch some links to point to the github repo
